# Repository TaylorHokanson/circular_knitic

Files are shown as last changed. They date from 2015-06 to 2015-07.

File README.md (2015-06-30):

Original design (c) 2014 Varvara Guljajeva & Mar Canet. See below for original Readme text.

Design changes/suggestions offered by Assistant Professors Taylor
Hokanson and Dieter Kirkwood, who are currently working on a build at
Columbia College Chicago. For more info on this and related machine
knitting projects, see
http://taylorhokanson.com/category/research/hardware/machine-knitting/

All files marked WIP = work in progress (unfinished) 

===============

Circular Knitic, an open hardware knitting machine. 
Project video: https://www.youtube.com/watch?v=-GFXAGRynNM

When building the machine, it is crucial to have the parts 3D printed precisely. Hence, print the parts in High Quality.
We have printed our machine with Ultimaker2, Makerbot Replicator 2, Makerbot Replicator 2x, and RepRapBcn+. Since reprap is not so preciase, some STL files are names as ...REP, which we have altered for that printer.

For laser cutting we have used 5mm and 6mm plexiglass. Use 6mm one for the gears, file gear-up.ai. For the rest use 5mm plexiglass.

We are doing workshops to build one or more machines in one day, if you are interested hosting a workshop please let us know:
varvarag@gmail.com  or mar.canet@gmail.com See photos from WeMake Milano Makerspace workshop done in February 2015: https://www.flickr.com/photos/mcanet/sets/72157650274803049/

Copyright (c) 2014 Varvara Guljajeva & Mar Canet

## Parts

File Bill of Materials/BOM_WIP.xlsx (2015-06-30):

Budget - Circular Knitic
description | real price | quantity | total | link
needles | €0.45 | 100 | €45.00 | http://www.bsk.co.uk/knitmastersilver-reed-sk120--sr120-xkn8-763-p.asp
stepper motor nema23 | €50.00 | 1 | €24.95 | https://www.pololu.com/product/1476 | DK
Big Easy stepper motor Driver | €20.00 | 1 | €19.95 | https://www.sparkfun.com/products/12859 | DK
Arduino Uno | €21.00 | 1 | €21.00
ventilator 12v 40mm x 40mm | €6.00 | 1 | €8.95 | http://www.jameco.com/webapp/wcs/stores/servlet/ProductDisplay?productId=1928118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 | DK
power supply 12v | €20.00 | 1 | €20.00
cabling | €8.00 | 1 | €8.00
carbon fiber tensor 2mm | €1.00 | 1 | €1.00 | http://www.mwmaterialsworld.com/es/barra-fibra-de-carbono.html | I think this is for the yarn tension unit. not needed
bearings (bore 5mm x 10mm x 4mm) | €0.60 | 14 | €16.00 | http://www.ebay.com/itm/10pcs-Axial-Ball-Thrust-Bearing-F5-10M-5mm-x-10mm-x-4mm-5-x-10-x-4-mm-/290699007785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 | DK
screws and nuts | €10.00 | 1 | €10.00
shaft of motor | €7.00 | 1 | €4.95 | http://www.pololu.com/product/2675 | DK
switch | €4.00 | 1 | €4.00
paper clips | €0.01 | 30 | €0.30
Plexiglas 5mm | €10.00 | 2 | €20.00 | http://proplastik.ee
Plexiglas 6mm | €11.00 | 1 | €11.00 | http://proplastik.ee
filament | €38.00 | 1 | €38.00
makerbeam 150mm | €2.20 | 2 | €4.40 | http://www.amazon.com/MakerBeam-200mm-beam-black-anodised/dp/B00G2DNTLQ?s=industrial | DK
makerbeam 60mm | €0.80 | 1 | €0.80 | included above
makerbeam 40mm | €0.60 | 1 | €0.60 | included above
makerbeam screws | €3.00 | 1 | €3.00 | 3d print these
makerbeam Lshape | €0.90 | 5 | €4.50 | http://www.amazon.com/MakerBeam-90-degree-brackets-pack/dp/B00G2DNV0U | BUY AT HOMEDEPOT? DK
wood structure | €25.00 | 1 | €25.00
claw weight | €6.00 | 4 | €24.00
paraphine | €2.00 | 1 | €2.00
 |  | Total | €334.00
Manufacturing
3d prints outers | €15.00 | 4 | €60.00
3d print inners | €6.00 | 24 | €144.00
3d print yarnholders | €12.00 | 4 | €48.00
3d print bearring holders | €3.00 | 5 | €15.00
3d print connectors | €1.00 | 15 | €15.00
Lasercutting | €90.00 | 0.5 | €45.00
 |  | Total | €327.00

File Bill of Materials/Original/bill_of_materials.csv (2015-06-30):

Budget - Circular Knitic
description | real price | quantity | total | link
needles | €0.45 | 100 | €45.00 | http://www.bsk.co.uk/knitmastersilver-reed-sk120--sr120-xkn8-763-p.asp
stepper motor nema23 | €50.00 | 1 | €50.00
Big Easy stepper motor Driver | €20.00 | 1 | €20.00
Arduino Uno | €21.00 | 1 | €21.00
ventilator 12v 40mm x 40mm | €6.00 | 1 | €6.00
power supply 12v | €20.00 | 1 | €20.00
cabling | €8.00 | 1 | €8.00
carbon fiber tensor 2mm | €1.00 | 1 | €1.00 | http://www.mwmaterialsworld.com/es/barra-fibra-de-carbono.html
bearings (bore 5mm x 10mm x 4mm) | €0.60 | 14 | €8.40
screws and nuts | €10.00 | 1 | €10.00
shaft of motor | €7.00 | 1 | €7.00 | http://www.pololu.com/product/2675
switch | €4.00 | 1 | €4.00
paper clips | €0.01 | 30 | €0.30
Plexiglas 5mm | €10.00 | 2 | €20.00 | http://proplastik.ee
Plexiglas 6mm | €11.00 | 1 | €11.00 | http://proplastik.ee
filament | €38.00 | 1 | €38.00
makerbeam 150mm | €2.20 | 2 | €4.40
makerbeam 60mm | €0.80 | 1 | €0.80
makerbeam 40mm | €0.60 | 1 | €0.60
makerbeam screws | €3.00 | 1 | €3.00
makerbeam Lshape | €0.90 | 5 | €4.50
wood structure | €25.00 | 1 | €25.00
claw weight | €6.00 | 4 | €24.00
paraphine | €2.00 | 1 | €2.00
 |  | Total | €334.00
Manufacturing
3d prints outers | €15.00 | 4 | €60.00
3d print inners | €6.00 | 24 | €144.00
3d print yarnholders | €12.00 | 4 | €48.00
3d print bearring holders | €3.00 | 5.00 | €15.00
3d print connectors | €1.00 | 15 | €15.00
Lasercutting | €90.00 | 0.5 | €45.00
 |  | Total | €327.00

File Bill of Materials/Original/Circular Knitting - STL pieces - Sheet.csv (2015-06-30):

comments | max layer height | Order nr. | Components | # of Pieces
1 and 2 are the same pieces. | 0.06 (recommended) | 1 | BearringBig1212 (repaired).stl | 1
this piece has been made slightly bigger for the reprap printer | 0.15 | 2 | BearringBigREP (repaired).stl | 1
 | 0.06 | 3 | BearringSmall1312 (repaired).stl | 4
 | 0.15 | 4 | Pipe (repaired).stl | 1
 | 0.15 | 5 | YarnHolderPalo.stl | 2
6 and 7 are the same | 0.06 | 6 | Zshape1212 (repaired).stl | 4
made for reprap | 0.15 | 7 | ZshapeRep (repaired).stl | 4
 | 0.1 | 8 | connection0912.stl | 11
 | 0.06 | 9 | inner0112 (repaired).stl | 12
 | 0.1 | 10 | mountain1212 (repaired).stl | 1
 | 0.15 | 11 | outer2511 (repaired).stl | 4
 | 0.1 | 12 | outerNeedleConnector (repaired).stl | 4
 | 0.1 | 13 | yarnHolder0212 (repaired).stl | 4
*print all parts in 'High Quality' (the option that your slicr program has).
Max layer height 0.1mm and infill 15% or 20%.
With layer height 0.06 no filing is required

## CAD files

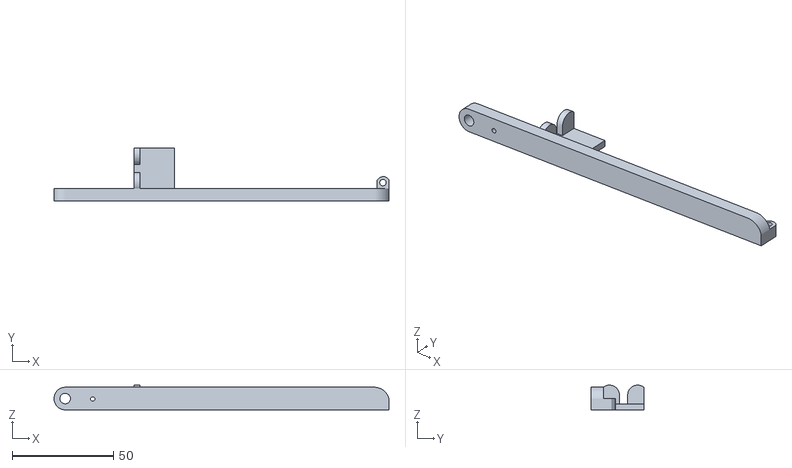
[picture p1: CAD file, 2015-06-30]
Fabrication/3D Printing/Original STLs/yarnTensioner1.stl
165.3 x 26.0 x 12.3

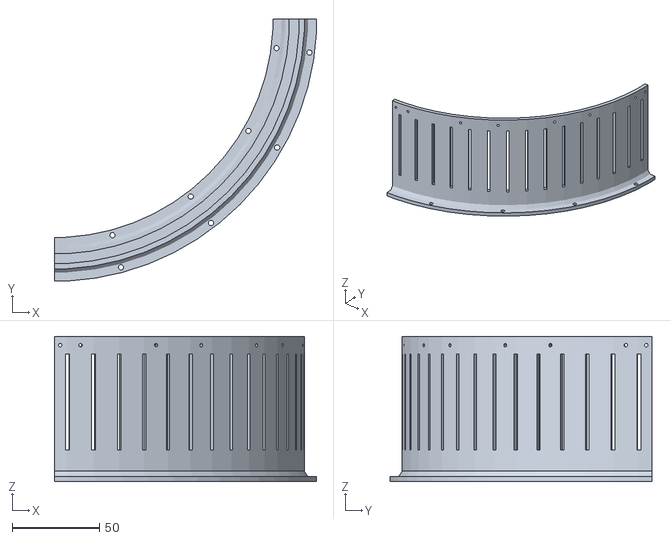
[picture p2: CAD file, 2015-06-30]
Fabrication/3D Printing/Original STLs/outer2511_x_4.stl
149.8 x 149.8 x 83.0

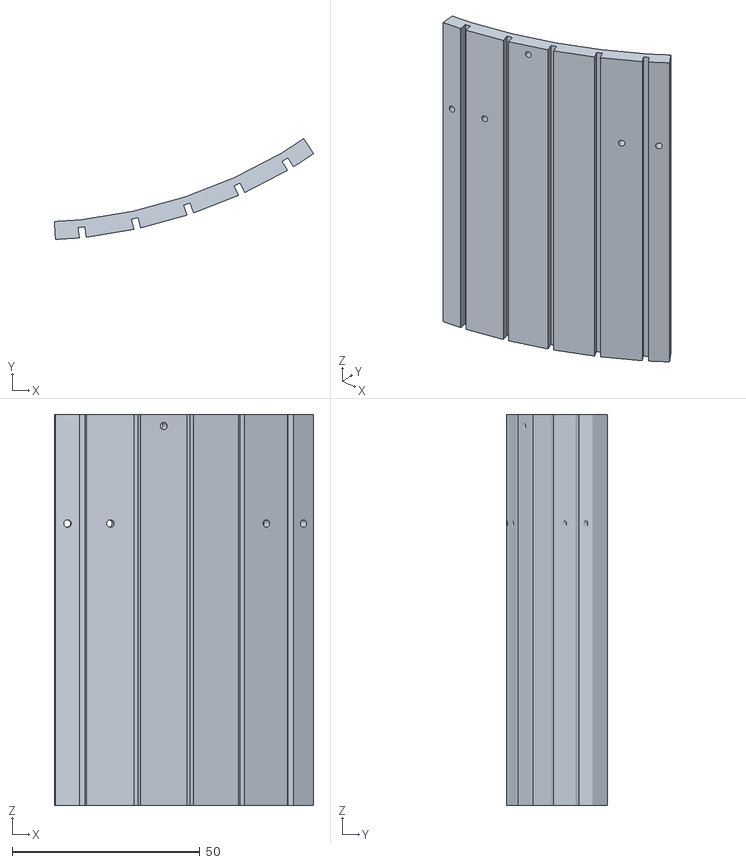
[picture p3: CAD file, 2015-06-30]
Fabrication/3D Printing/Original STLs/inner0112_x_12.stl
69.0 x 26.8 x 104.0

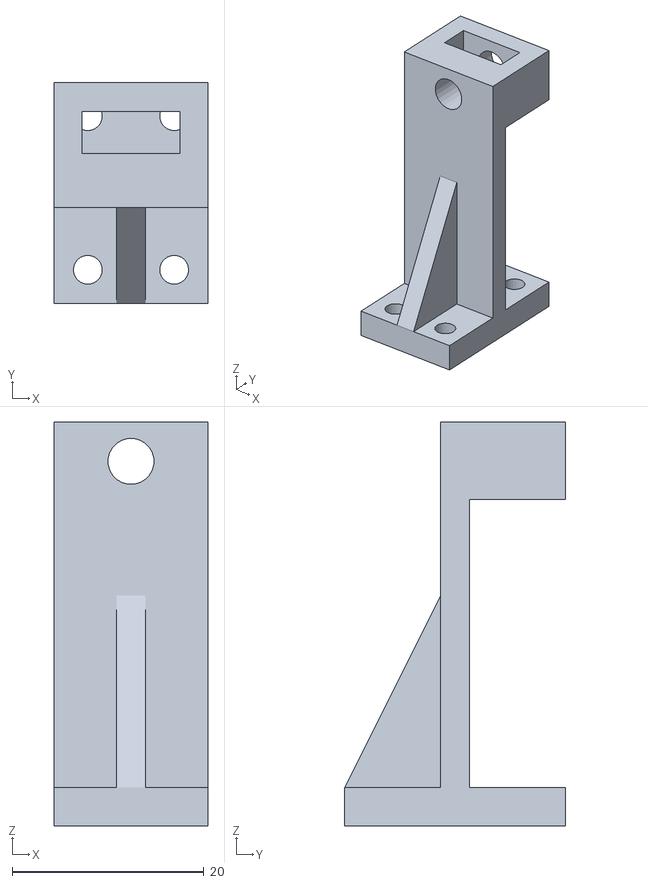
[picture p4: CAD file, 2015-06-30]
Fabrication/3D Printing/Original STLs/Zshape1212_x_4.stl
16.0 x 23.0 x 42.1

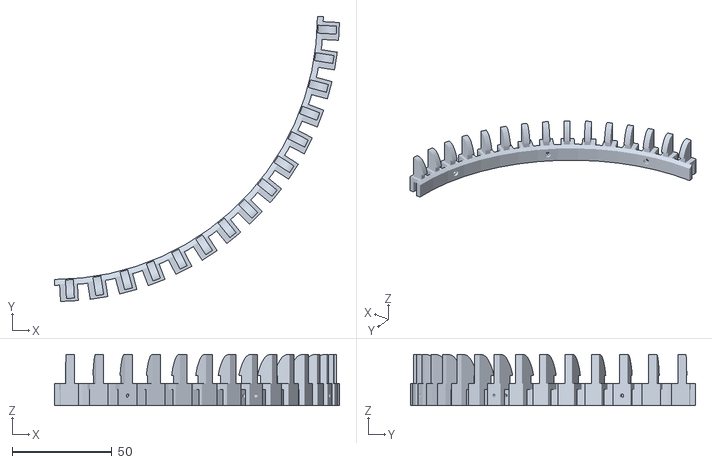
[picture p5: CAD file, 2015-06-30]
Fabrication/3D Printing/Original STLs/yarnHolder0212_x_4.stl
142.9 x 142.9 x 25.6

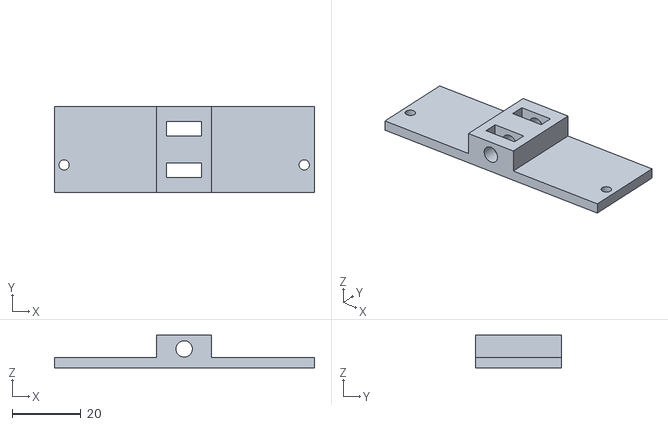
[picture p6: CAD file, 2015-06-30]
Fabrication/3D Printing/Original STLs/BearringBig1212 (repaired).stl
75.8 x 25.0 x 9.50

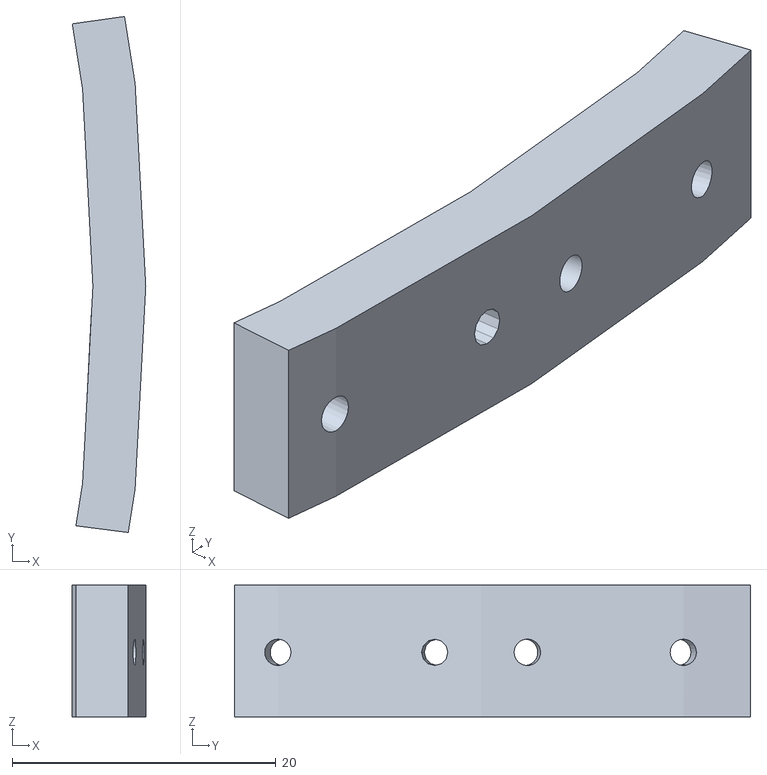
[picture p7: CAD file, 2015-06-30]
Fabrication/3D Printing/Original STLs/outerConnector_x_4.stl
5.57 x 39.1 x 10.0

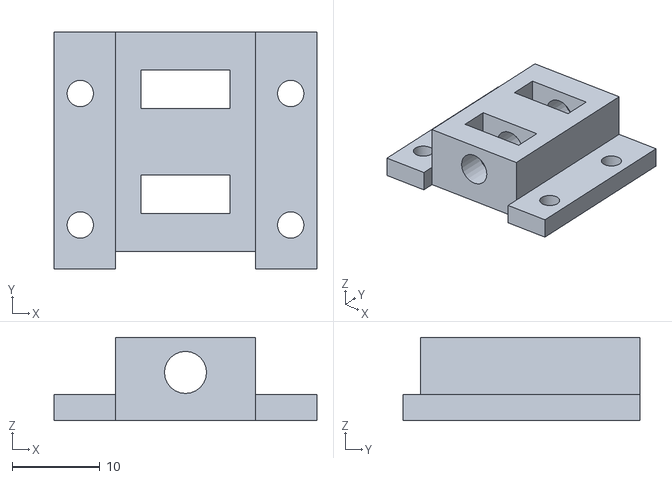
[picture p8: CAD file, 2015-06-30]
Fabrication/3D Printing/Original STLs/BearringSmall1312_x_4.stl
30.0 x 27.0 x 9.50

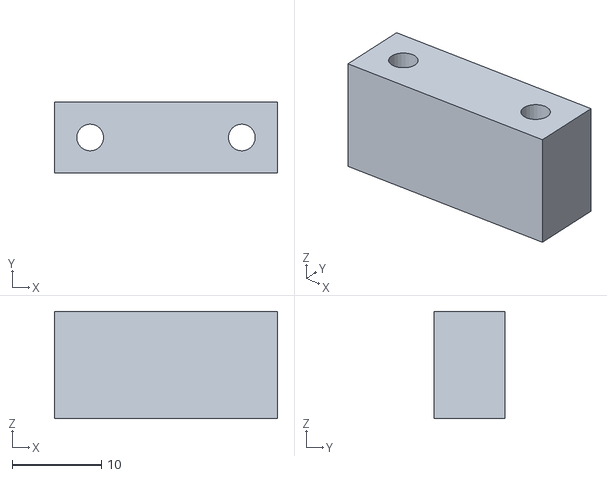
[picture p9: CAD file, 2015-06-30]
Fabrication/3D Printing/Original STLs/connection0912_x_11.stl
25.0 x 8.00 x 12.0

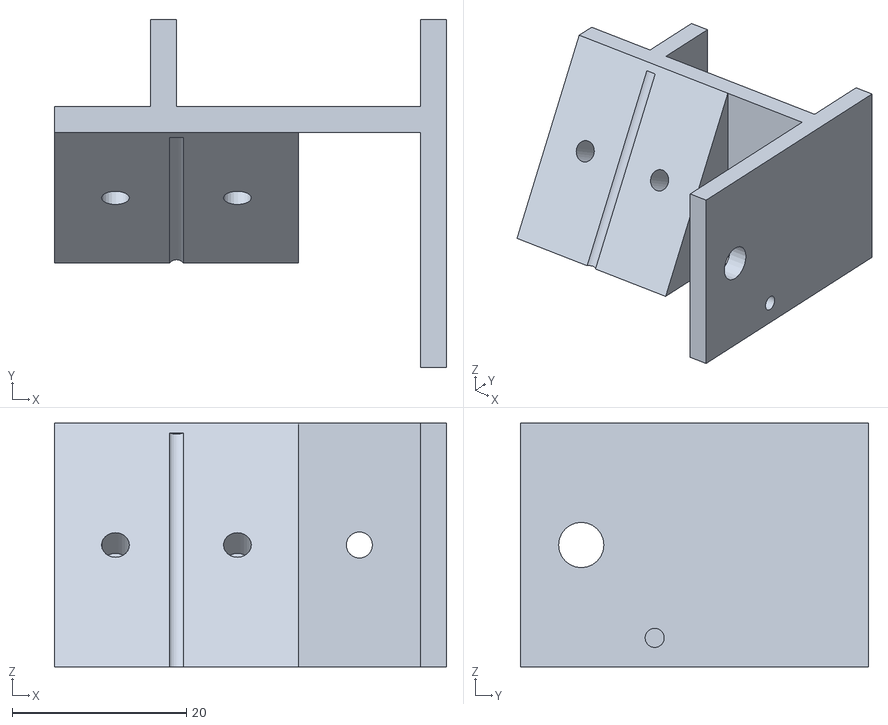
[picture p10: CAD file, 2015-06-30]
Fabrication/3D Printing/Original STLs/yarnfeederSupport.stl
45.0 x 40.0 x 28.0

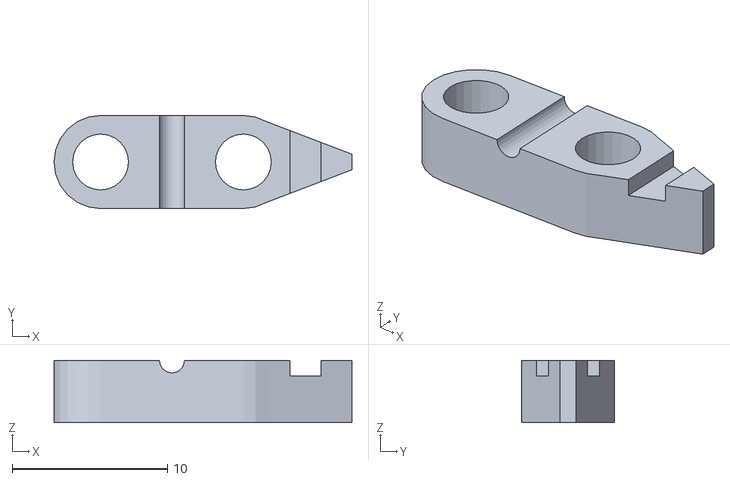
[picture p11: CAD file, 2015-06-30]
Fabrication/3D Printing/Original STLs/YarnHolderPalo_x_2.stl
19.2 x 6.00 x 4.00

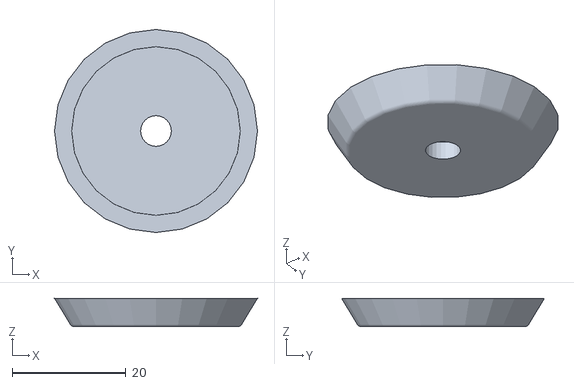
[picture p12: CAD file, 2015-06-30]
Fabrication/3D Printing/Original STLs/spring.stl
35.7 x 35.7 x 5.00

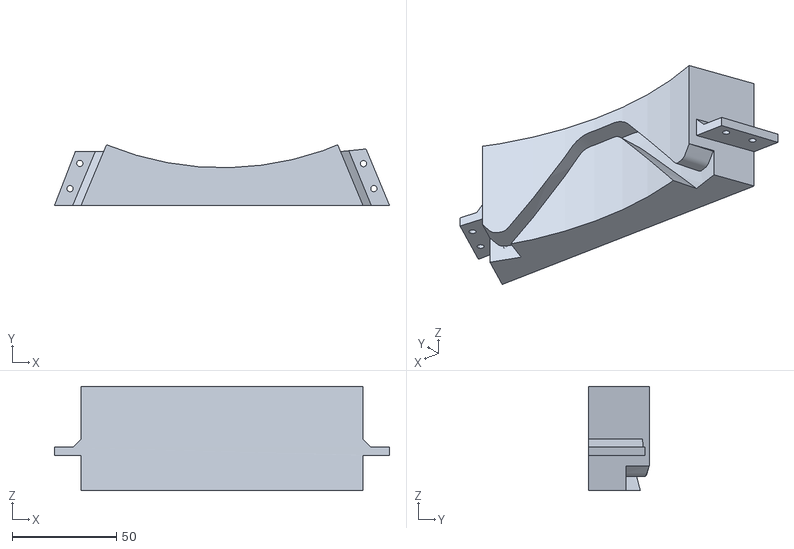
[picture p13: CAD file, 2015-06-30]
Fabrication/3D Printing/Original STLs/mountain1212 (repaired).stl
160.9 x 29.1 x 50.0

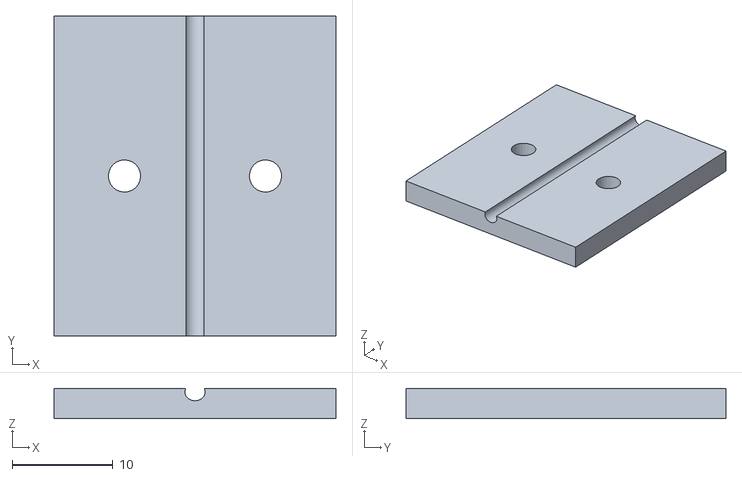
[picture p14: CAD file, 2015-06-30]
Fabrication/3D Printing/Original STLs/YarnTensonerHolder300315.stl
28.0 x 31.8 x 3.00

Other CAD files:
Fabrication/3D Printing/Original STLs/ZshapeRep_x_4.stl
Fabrication/3D Printing/Original STLs/BearringBigREP (repaired).stl
Fabrication/3D Printing/3DM/1.3dm
Fabrication/3D Printing/3DM/2.3dm
Fabrication/3D Printing/3DM/3.3dm
Fabrication/3D Printing/3DM/4.3dm
Fabrication/3D Printing/3DM/5_WIP.3dm
Fabrication/3D Printing/3DM/6.3dm
Fabrication/3D Printing/3DM/Mountain.3dm
_CircularKnitic.skp

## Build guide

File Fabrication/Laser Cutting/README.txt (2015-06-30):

All cuts made in 5.5mm/.25" acrylic
Cut order is Red, Green, Blue
You only need one gear, but we cut extras because they kept breaking teeth before everything was lubed and running smoothly

Changes:
All cuts distributed in the layers of one document
Color coded cut order
Deleted unused gears (for our BOM)
Deleted electronics housing (will post a different solution)
Reoriented stepper motor mount, control panel

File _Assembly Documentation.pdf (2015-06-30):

open source knitting machine
http://var-mar.info | http://www.knitic.com

Varvara Guljajeva & Mar Canet

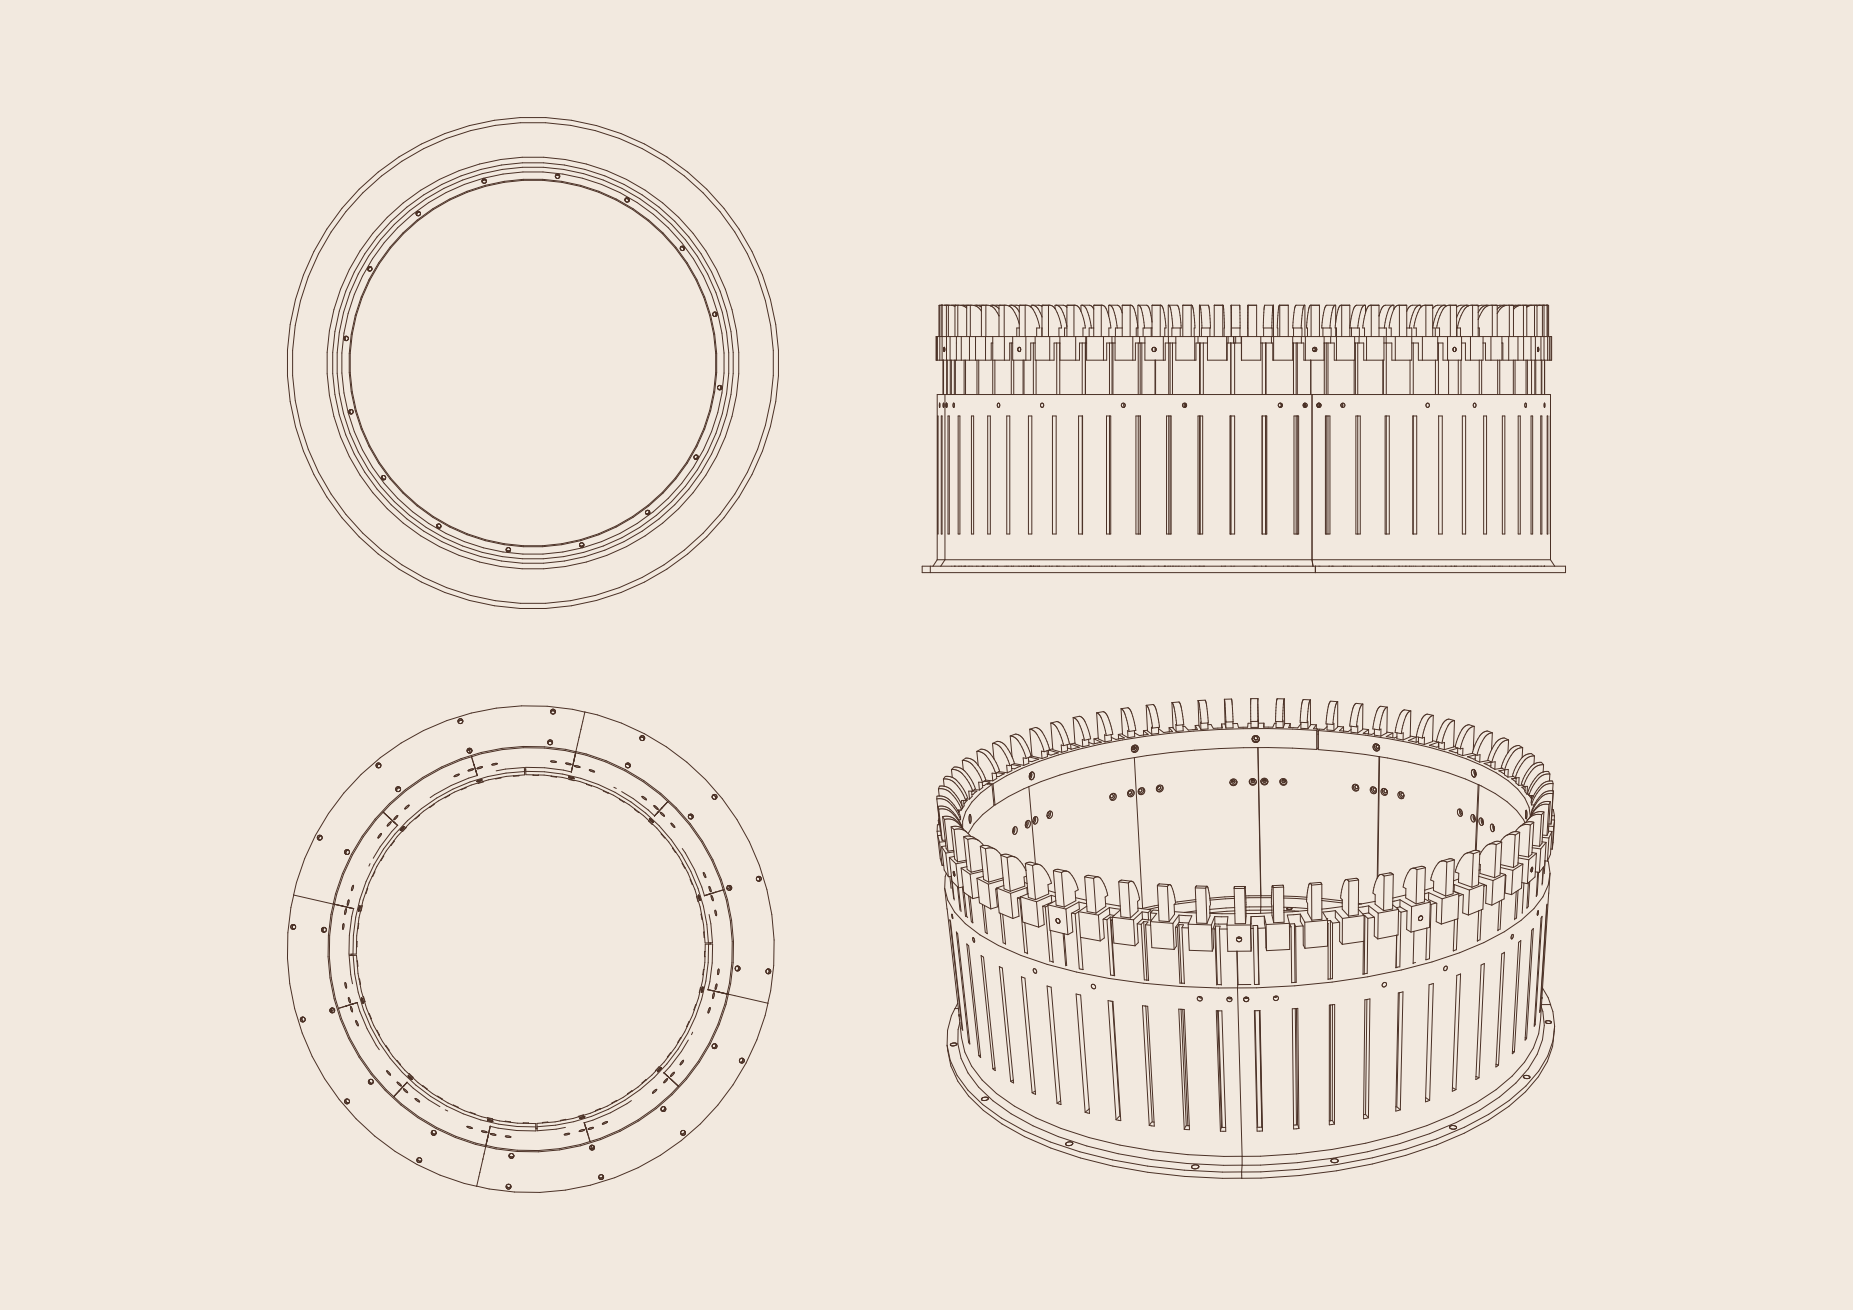
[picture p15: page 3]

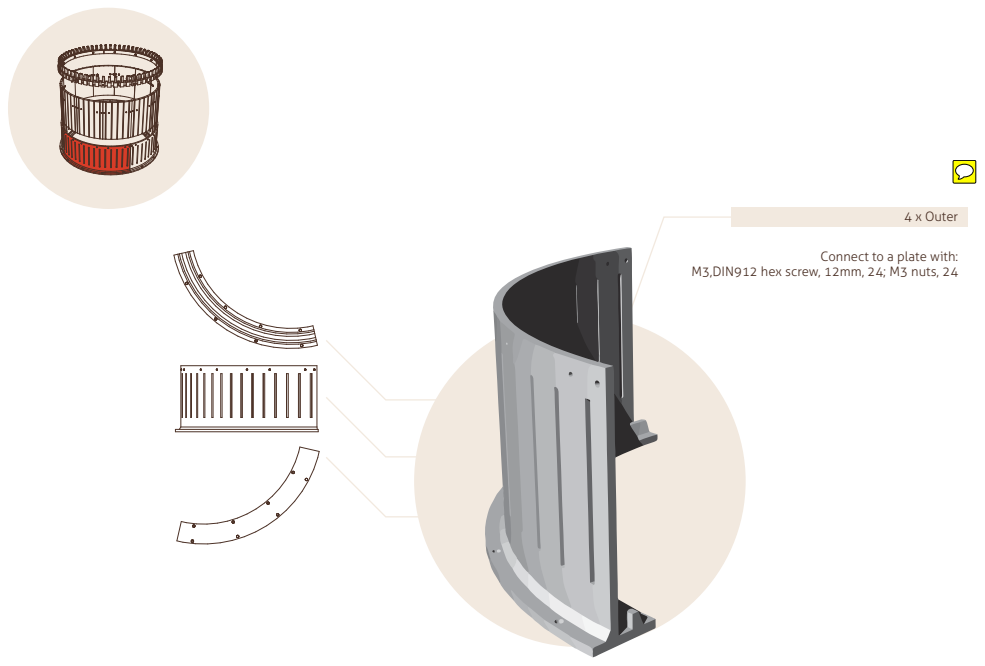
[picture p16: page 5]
4 x Outer

Connect to a plate with:

M3,DIN912 hex screw, 12mm, 24; M3 nuts, 24

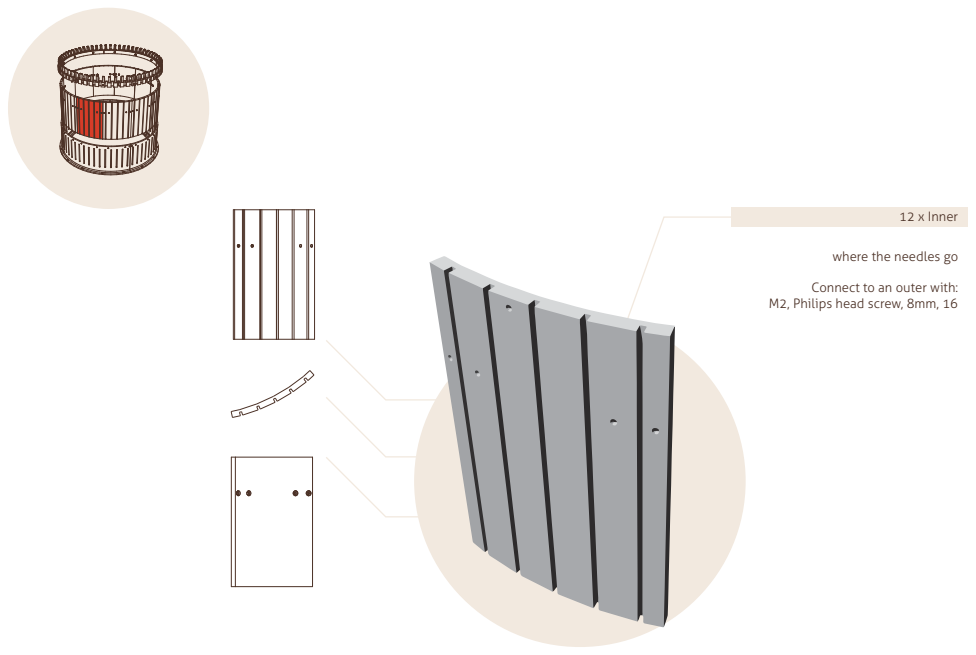
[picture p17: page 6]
12 x Inner

where the needles go

Connect to an outer with:
M2, Philips head screw, 8mm, 16

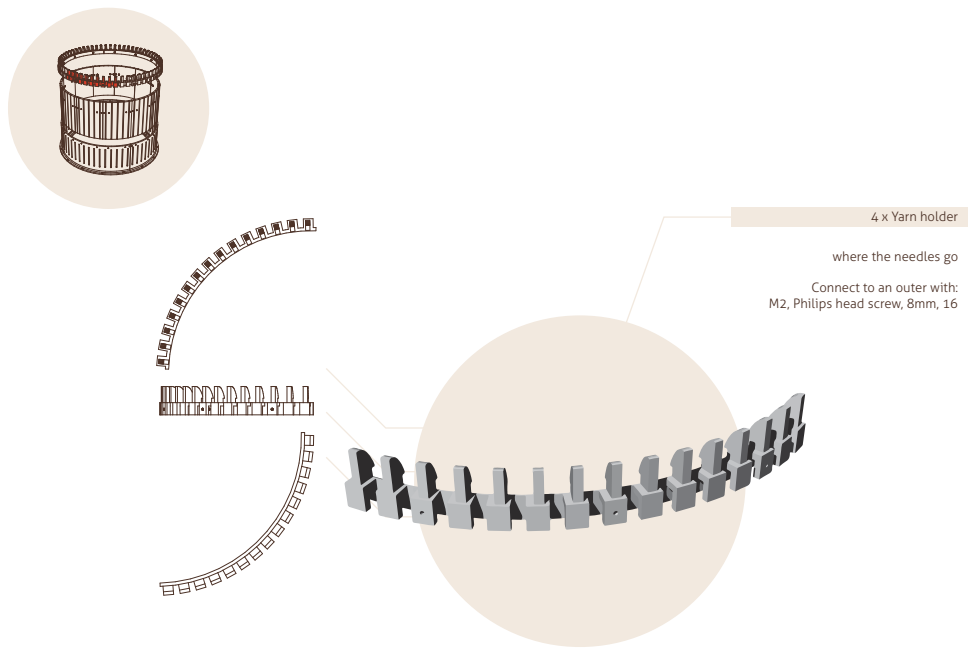
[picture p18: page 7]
4 x Yarn holder

where the needles go

Connect to an outer with:
M2, Philips head screw, 8mm, 16

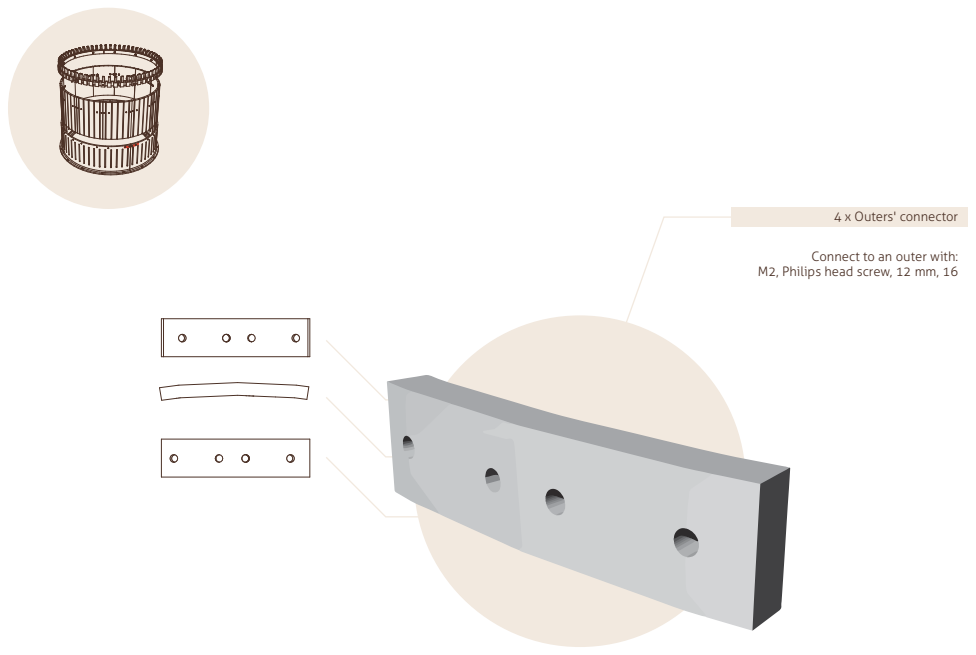
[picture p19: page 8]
4 x Outers' connector

Connect to an outer with:

M2, Philips head screw, 12 mm, 16

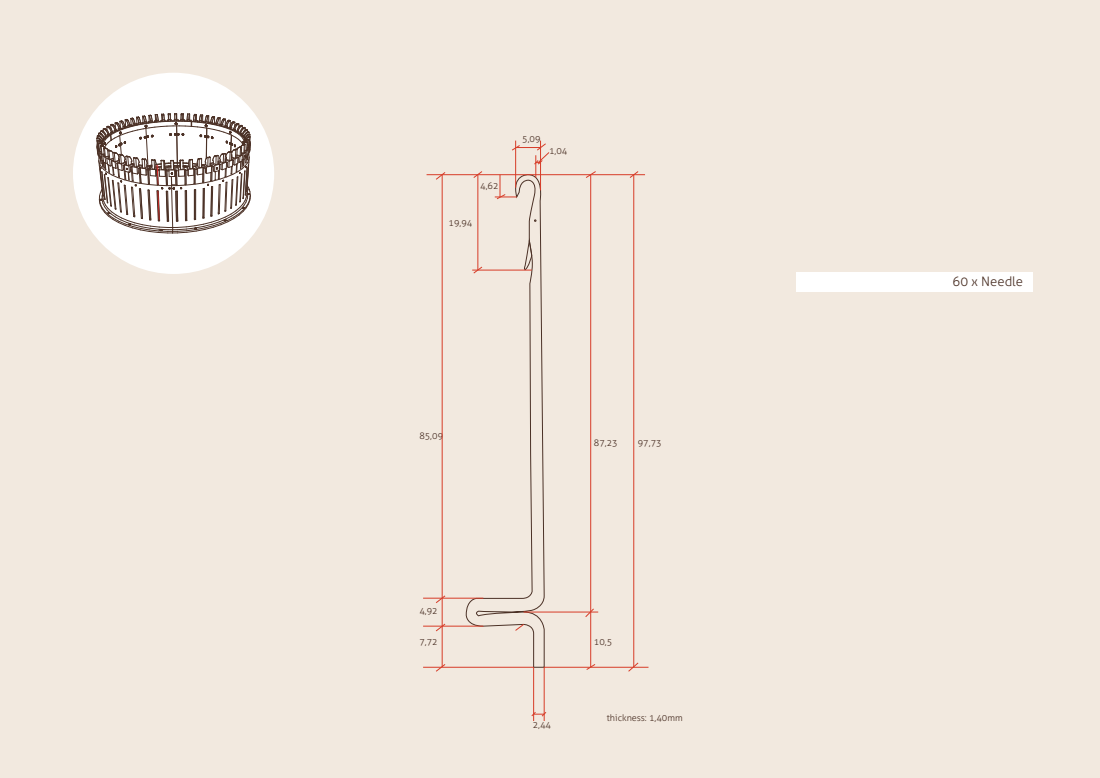
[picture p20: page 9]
60 x Needle; thickness: 1,40mm

Bottom surface (big gear) + motor gears

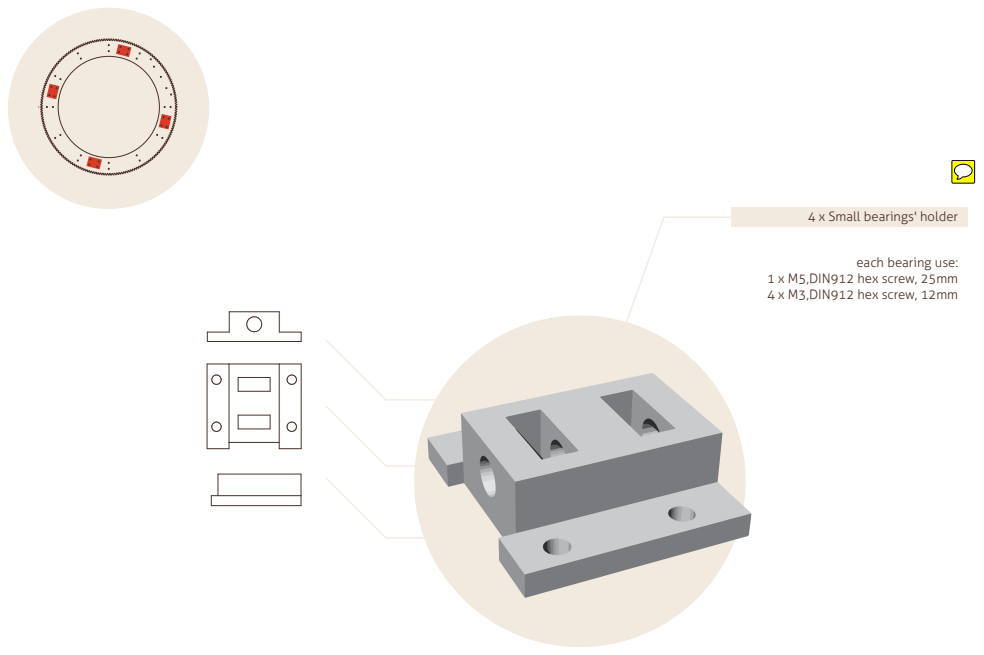
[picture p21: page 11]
1 x M5,DIN912 hex screw, 25mm 4 x M3,DIN912 hex screw, 12mm

4 x Small bearings' holder

each bearing use:

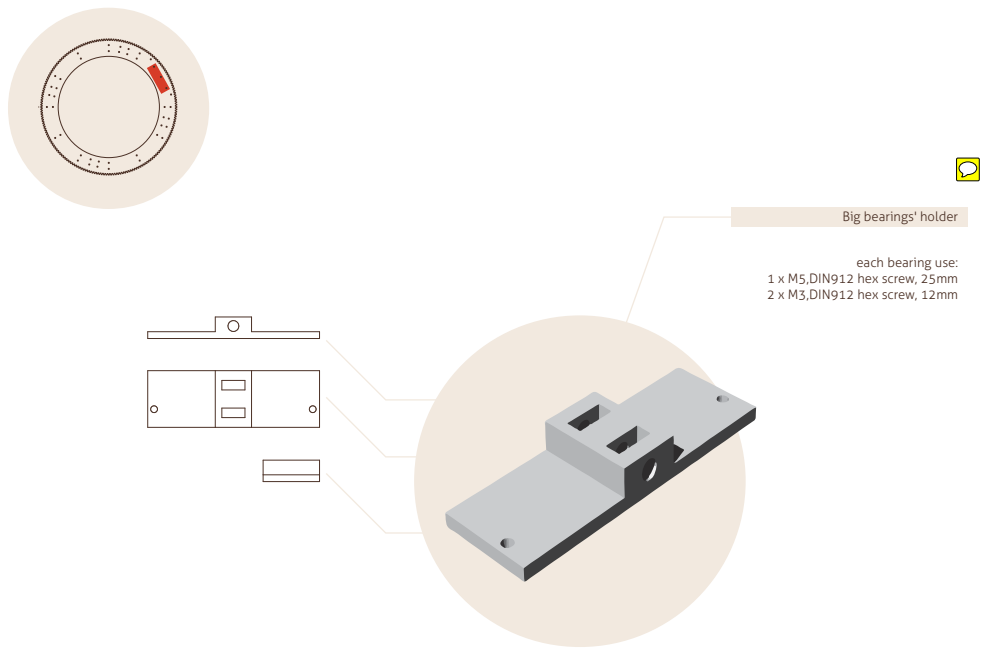
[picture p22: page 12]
1 x M5,DIN912 hex screw, 25mm 2 x M3,DIN912 hex screw, 12mm

Big bearings' holder

each bearing use:

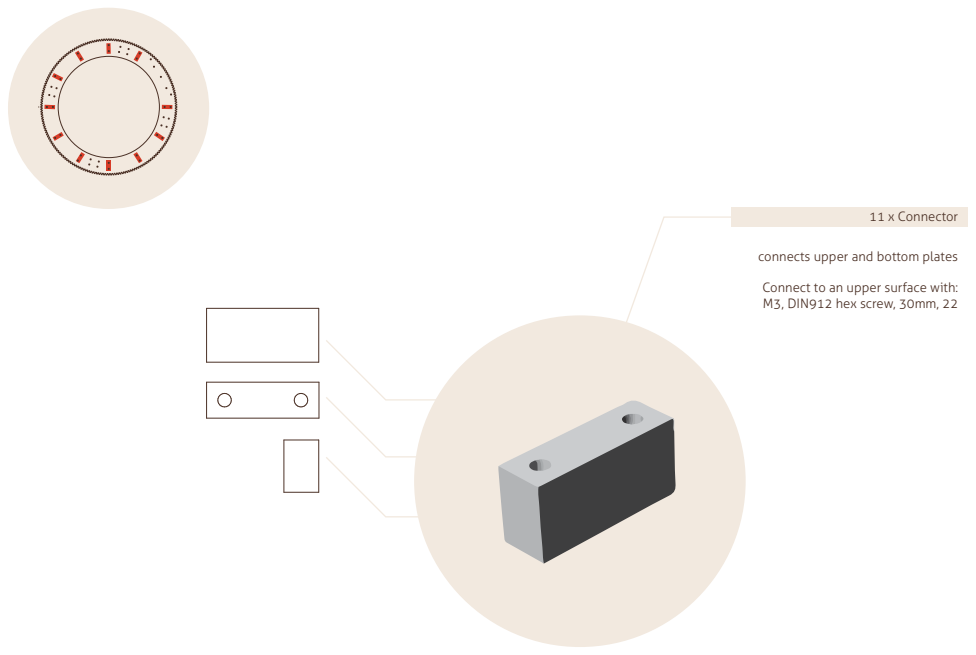
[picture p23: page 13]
11 x Connector

connects upper and bottom plates

Connect to an upper surface with:
M3, DIN912 hex screw, 30mm, 22

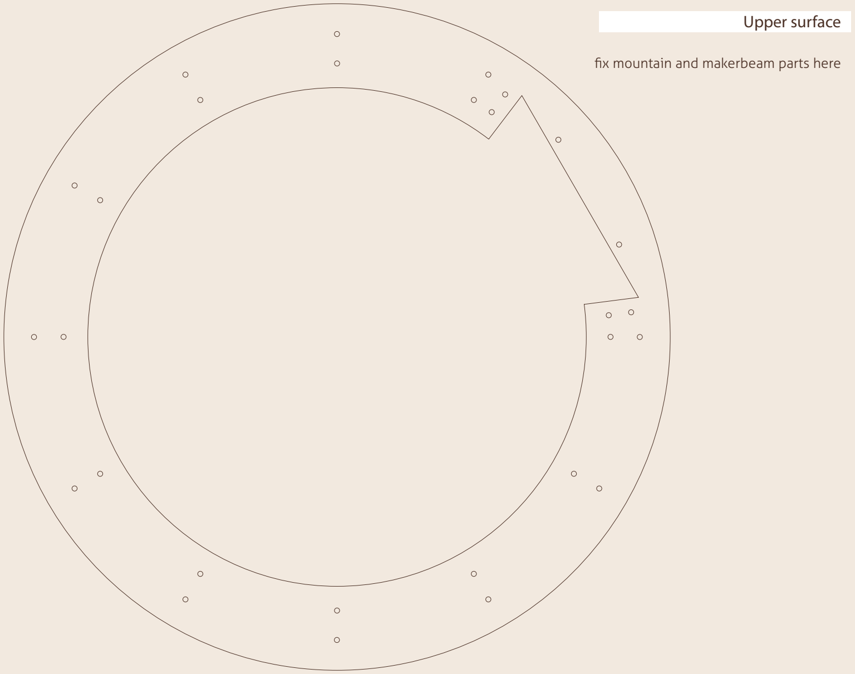
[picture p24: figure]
fix mountain and makerbeam parts here; Upper surface
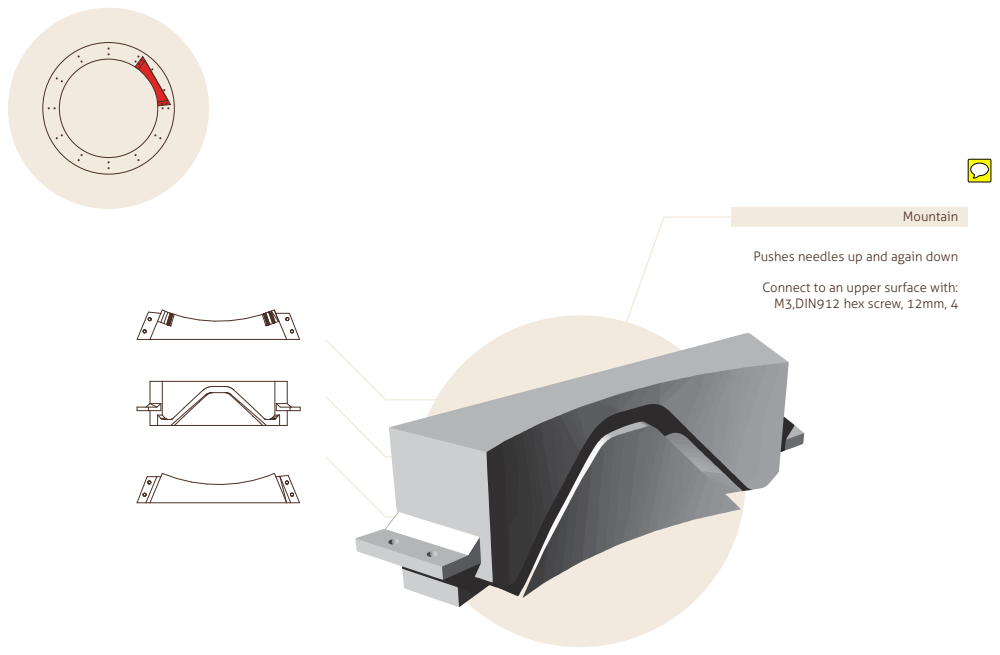
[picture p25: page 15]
Mountain

Pushes needles up and again down

Connect to an upper surface with:
M3,DIN912 hex screw, 12mm, 4

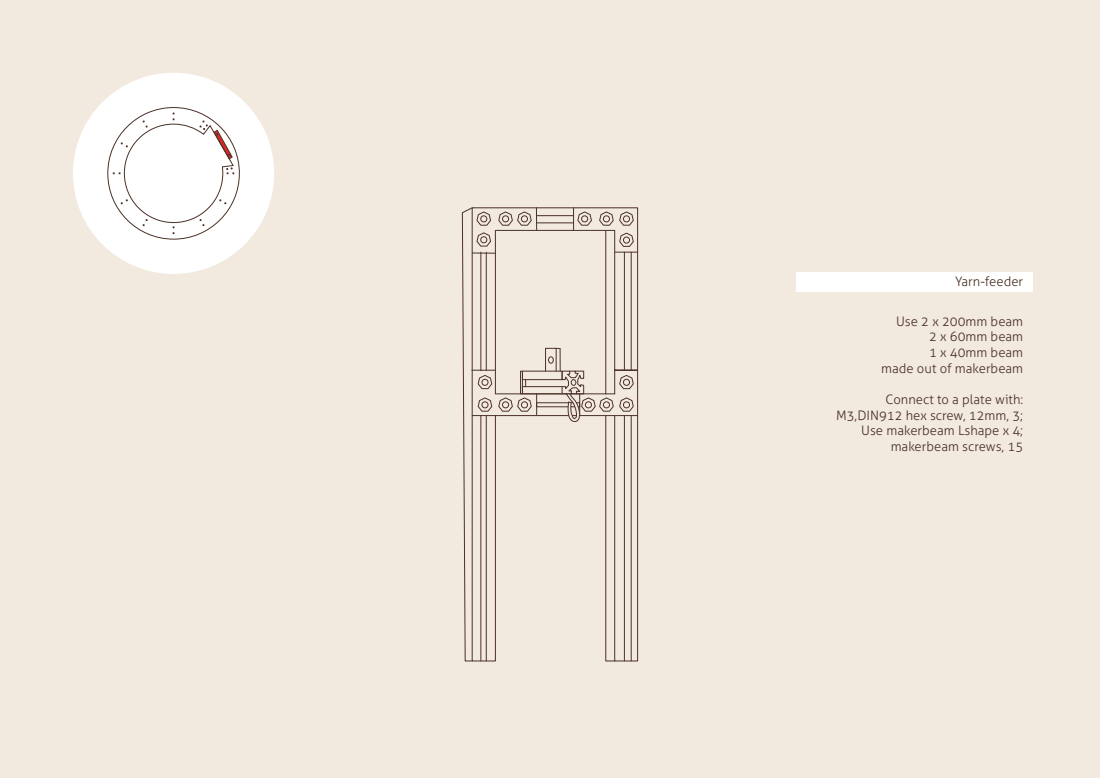
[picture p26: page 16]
Use 2 x 200mm beam 2 x 60mm beam 1 x 40mm beam; Yarn-feeder

made out of makerbeam

Connect to a plate with:

M3,DIN912 hex screw, 12mm, 3;
Use makerbeam Lshape x 4;
makerbeam screws, 15

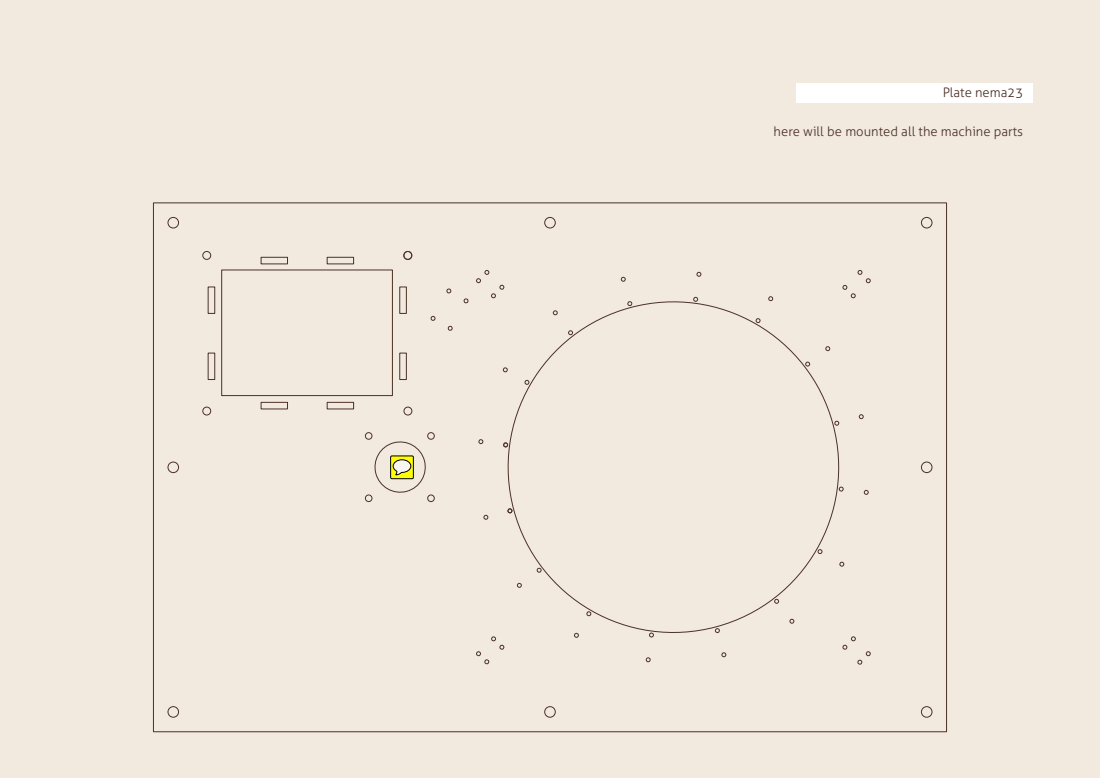
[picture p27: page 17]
Plate nema23

here will be mounted all the machine parts

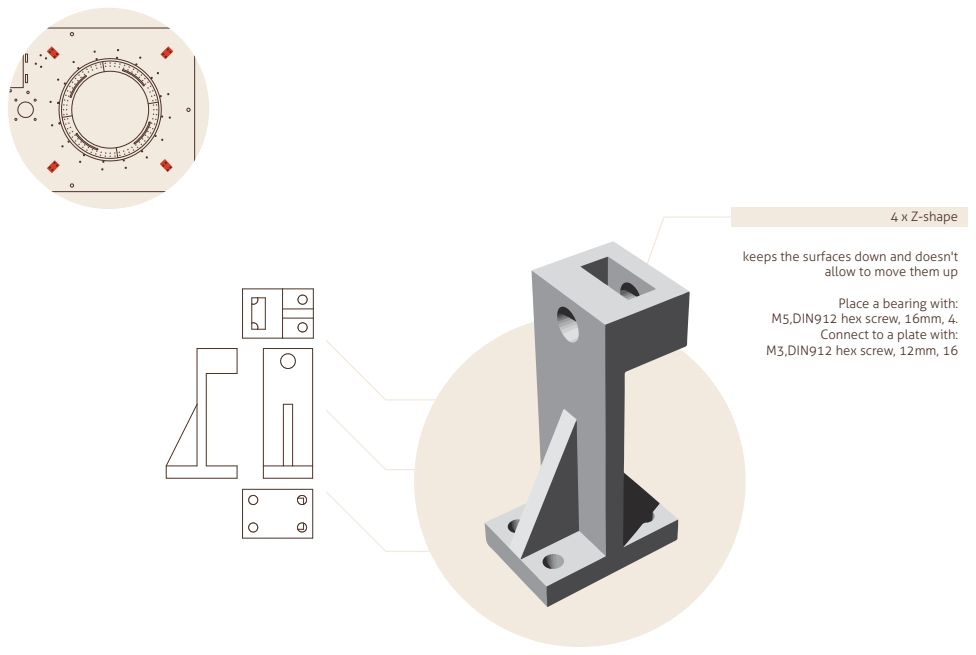
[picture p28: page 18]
M5,DIN912 hex screw, 16mm, 4.; M3,DIN912 hex screw, 12mm, 16; 4 x Z-shape

keeps the surfaces down and doesn't

allow to move them up

Place a bearing with:

Connect to a plate with:

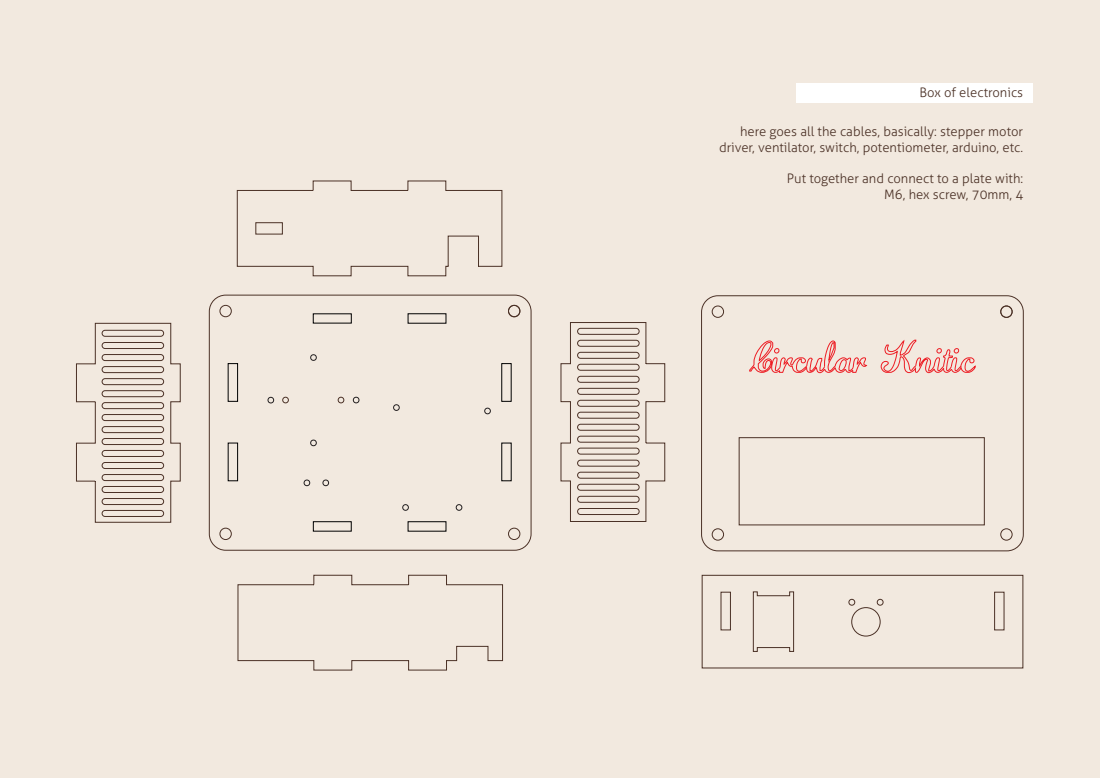
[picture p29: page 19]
M6, hex screw, 70mm, 4

Box of electronics

here goes all the cables, basically: stepper motor
driver, ventilator, switch, potentiometer, arduino, etc.

Put together and connect to a plate with:

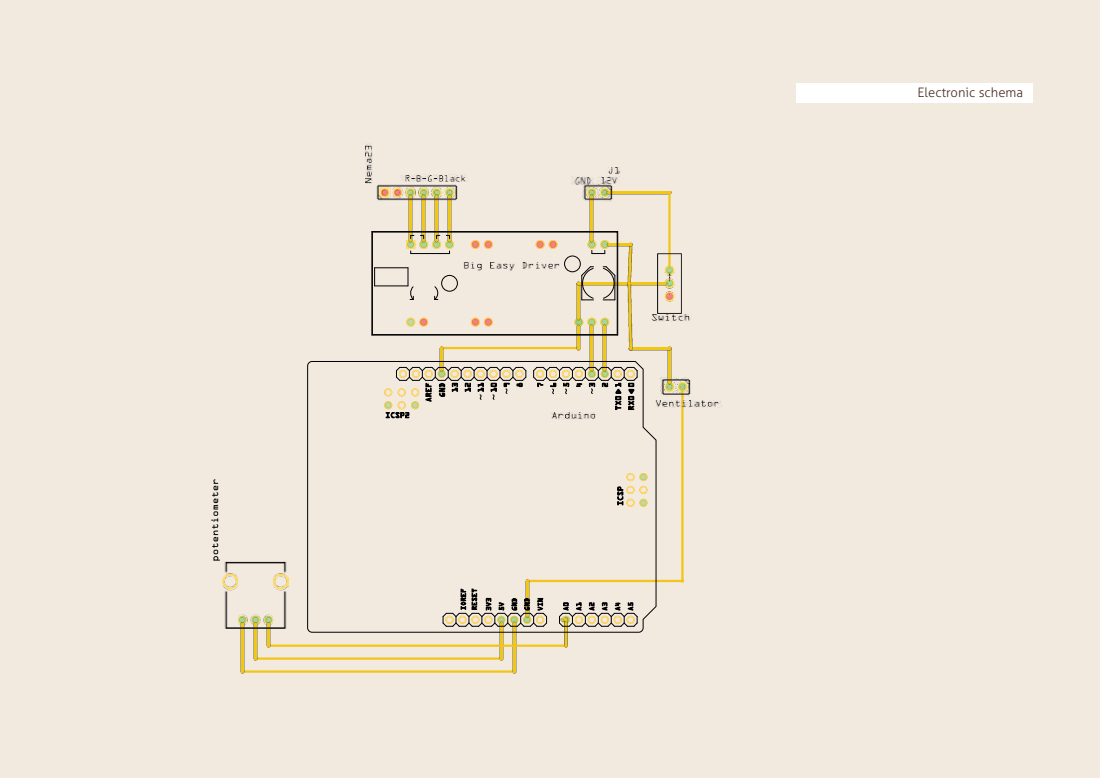
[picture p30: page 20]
Electronic schema

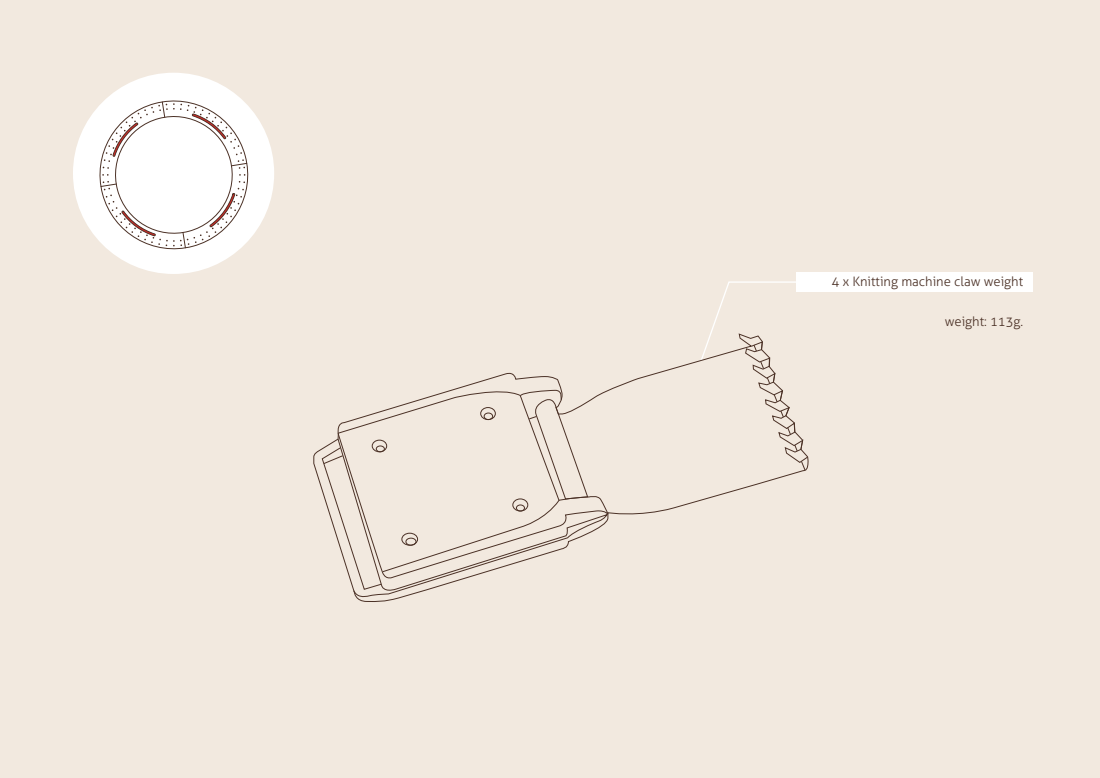
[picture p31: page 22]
weight: 113g.

4 x Knitting machine claw weight

this item fixes a stick, which brings yarn

to the machine, into the table

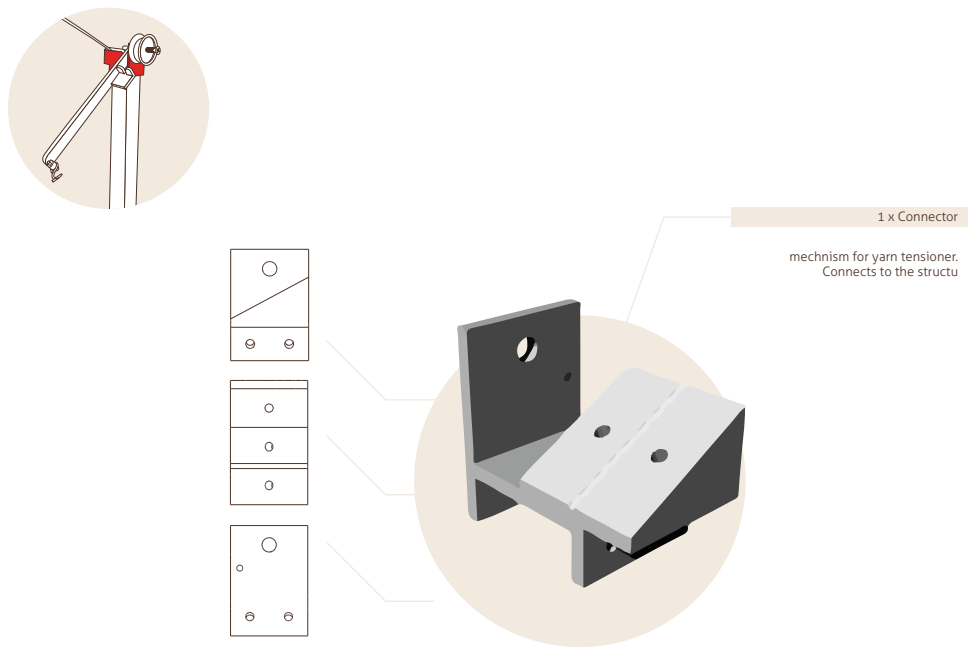
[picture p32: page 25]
1 x Connector

mechnism for yarn tensioner.
Connects to the structu

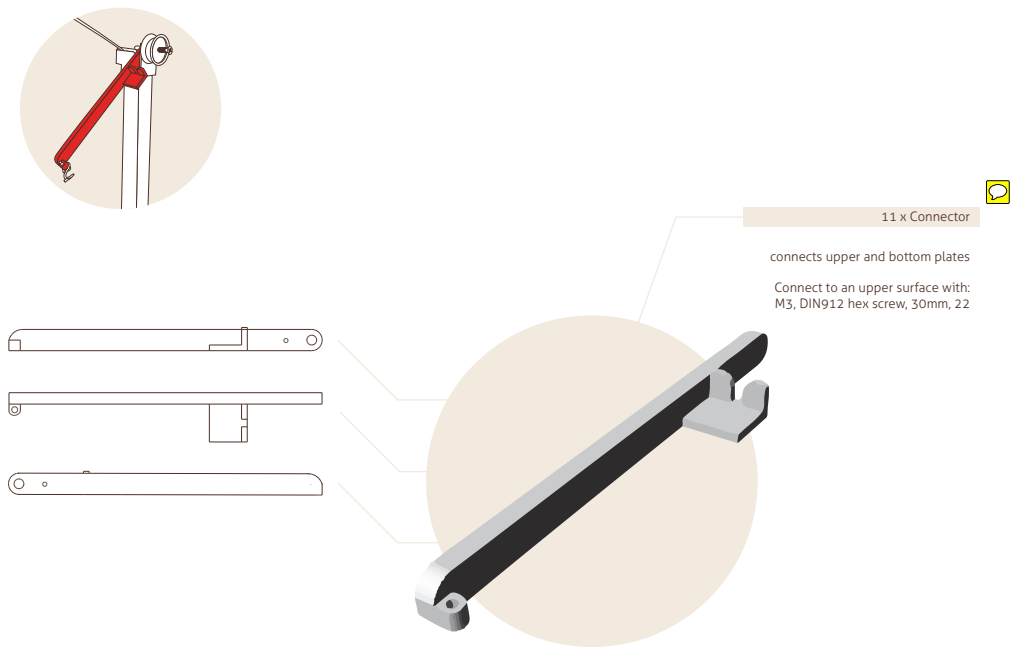
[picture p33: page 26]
11 x Connector

connects upper and bottom plates

Connect to an upper surface with:
M3, DIN912 hex screw, 30mm, 22

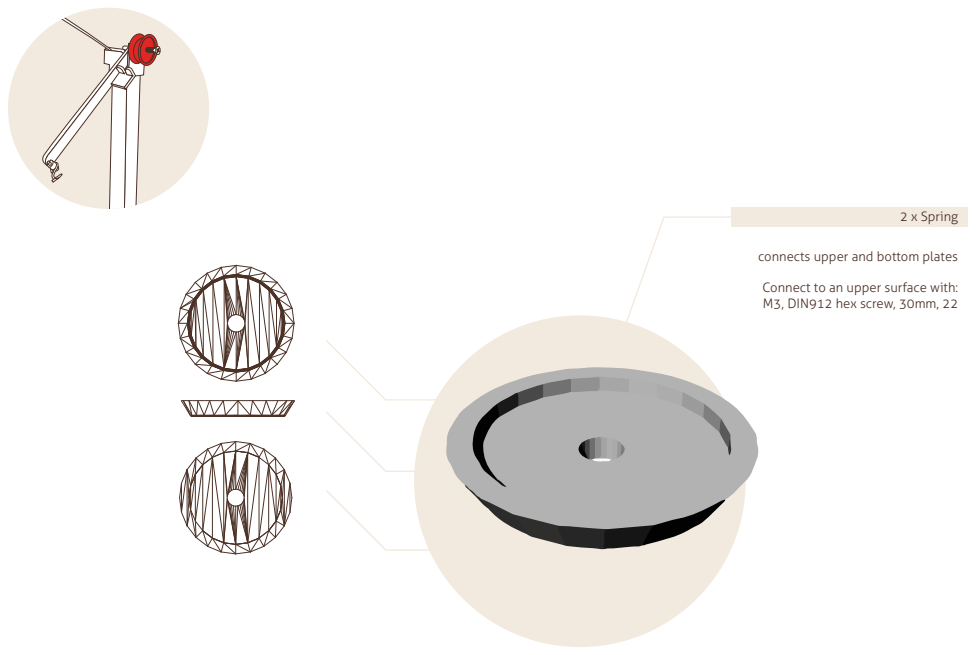
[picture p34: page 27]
2 x Spring

connects upper and bottom plates

Connect to an upper surface with:
M3, DIN912 hex screw, 30mm, 22

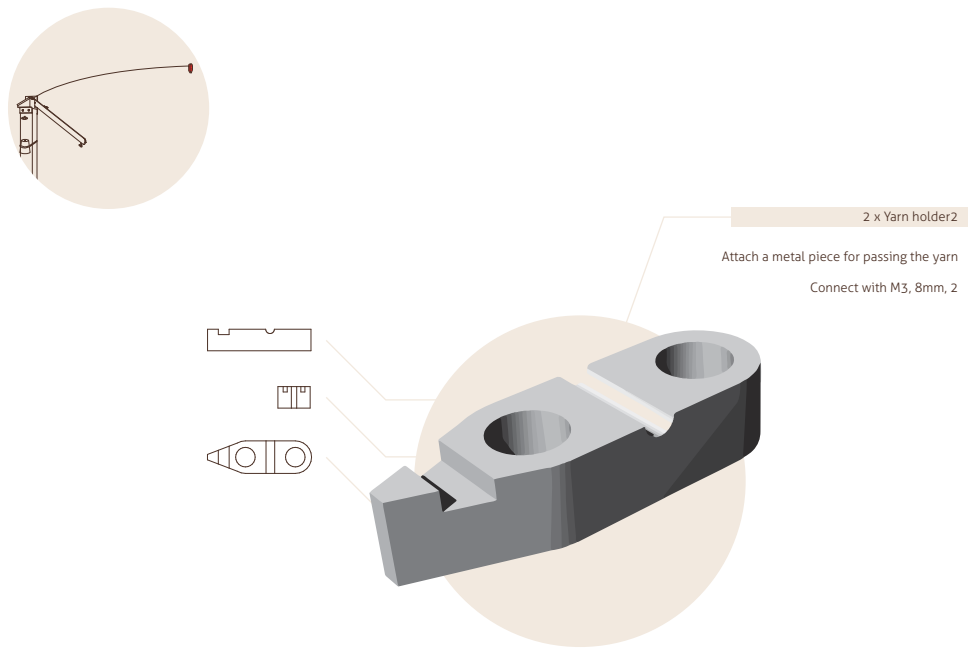
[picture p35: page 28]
Connect with M3, 8mm, 2; 2 x Yarn holder2

Attach a metal piece for passing the yarn

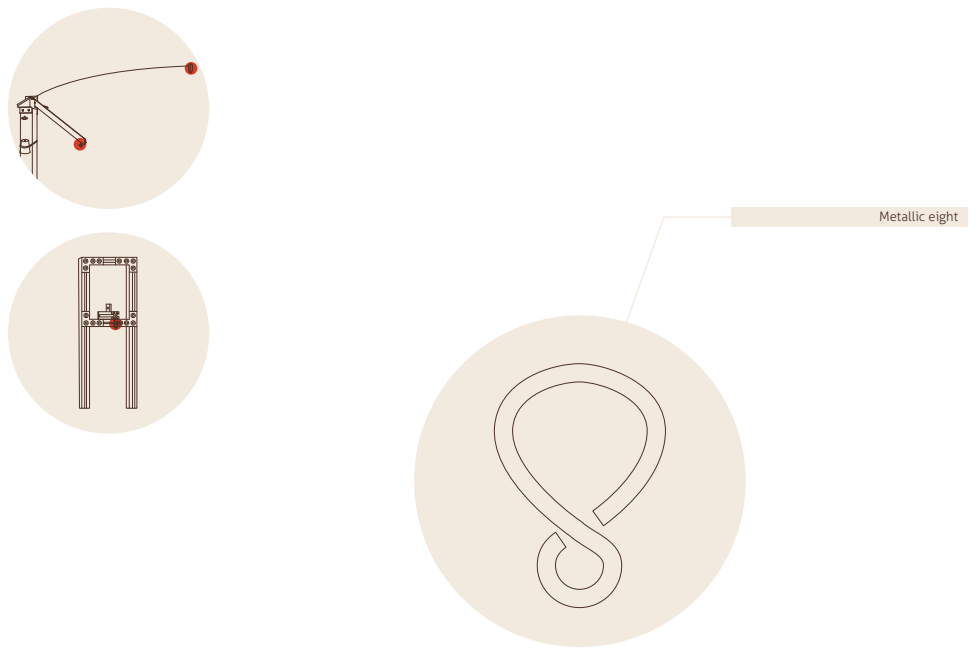
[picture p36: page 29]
Metallic eight

thickness: plate and surfaces

Bottom surface (big gear)

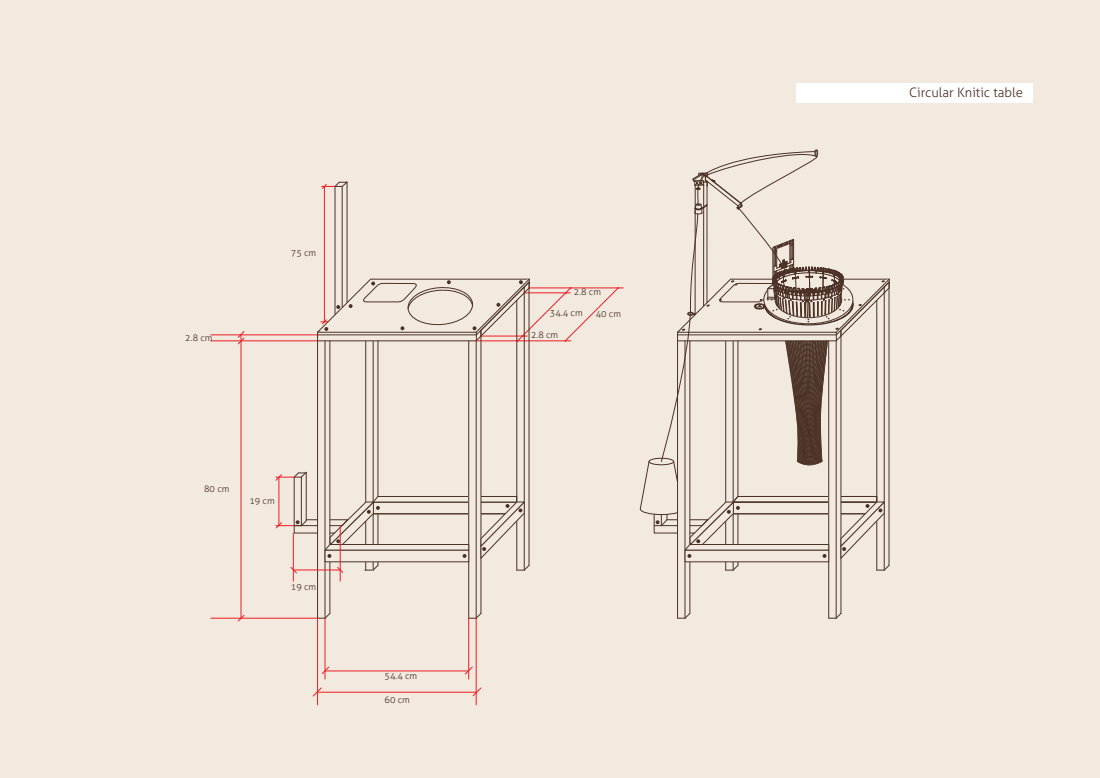
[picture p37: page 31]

Circular Knitic table

### Wood parts to create the machine frame

Other parts

Screws circular Knitic

Others

Size

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
Type

Philips head screw
Philips head screw
steel nut

Screw button head socket
DIN912 hex screw

DIN912 hex screw
DIN912 hex screw
steel nut

DIN912 hex screw
DIN912 hex screw
steel nylon lock nut
Philips head

hex screw
steel nut
wing steel nut

hospa screws

metallic angle | 30x30 x 15 x 2cm | mount wood frame

Long

8mm
12 mm

6mm
12mm

16mm
30mm

16mm
25mm

50mm

70mm

20mm

Quantity

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
attach inners with outer
attach inners with outer connections, yarn holders

makerbeam
attach outers to plexi, and z-shape, small and big bearings’ holders, mountain, construction from makerbeam
attach gear on the stepper motor
attach gear wheel with spacers

attach stepper motor
attach bearing

mount the electronic box
mount the electronic box
mount the electronic box

mount wood frame

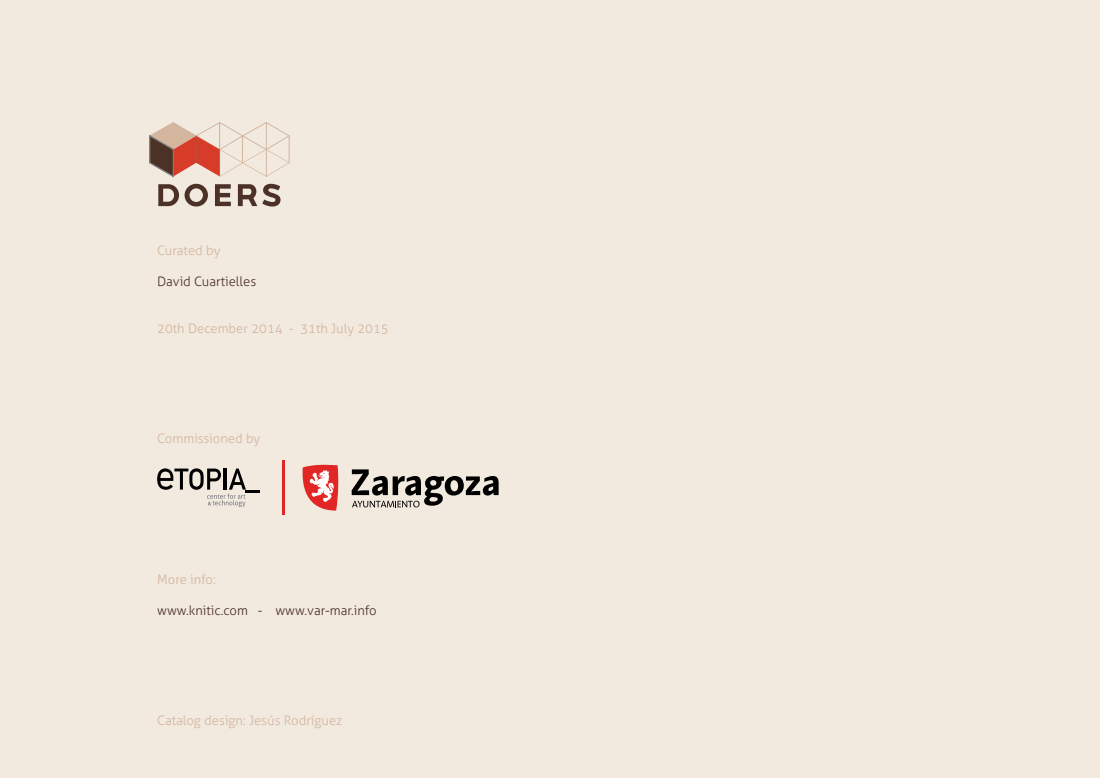
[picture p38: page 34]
Curated by; David Cuartielles; 20th December 2014 - 31th July 2015; Commissioned by; More info:

www.knitic.com - www.var-mar.info

Catalog design: Jesús Rodríguez

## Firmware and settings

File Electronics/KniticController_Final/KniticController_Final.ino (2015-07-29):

// Circular Knitic Controller
// Taylor Hokanson and Dieter Kirkwood
// based on the work of Varvara Guljajeva & Mar Canet

// Button (not implemented): GND > Momentary > Pin 12
// Potentiometer: left pin GND, center pin A0, right pin 5VDC
// Encoder: left pin 3, center pin 2, right pin GND

// Encoder
#include <Encoder.h>
Encoder eKnob(2, 3);
long oldKnobPos  = -999;
long newKnobPos = 0;

// Pot
int newPotVal;
int oldPotVal;
int motorSpeed = 0;
int motorJam = 0;

// Button
const int buttonPin = 12;    // the number of the pushbutton pin
const int ledPin = 13;      // the number of the LED pin
int ledState = LOW;          // start button state LOW (motor forward)
int buttonState;             // the current reading from the input pin
int lastButtonState = LOW;   // the previous reading from the input pin
long lastDebounceTime = 0;  // the last time the output pin was toggled
long debounceDelay = 50;    // the debounce time; increase if the output flickers

//Declare pin functions on Arduino
#define stp 7
#define dir 6
#define MS1 10
#define MS2 9
#define MS3 8
#define EN  11

void setup() {

  // Button
  pinMode(buttonPin, INPUT_PULLUP);
  pinMode(ledPin, OUTPUT);
  digitalWrite(ledPin, ledState);
  
  pinMode(stp, OUTPUT);
  pinMode(dir, OUTPUT);
  pinMode(MS1, OUTPUT);
  pinMode(MS2, OUTPUT);
  pinMode(MS3, OUTPUT);
  pinMode(EN, OUTPUT);
  resetBEDPins();           // Set step, direction, microstep and enable pins to default states

  // Pot
  ADCSRA = 0;
  ADCSRB = 0;
  ADMUX |= (1 << REFS0);                    //set reference voltage
  ADMUX |= (1 << ADLAR);                    //left align the ADC value- so we can read highest 8 bits from ADCH register only
  ADCSRA |= (1 << ADPS2) | (1 << ADPS0);    //set ADC clock with 32 prescaler- 16mHz/32=500kHz
  ADCSRA |= (1 << ADATE);                   //enabble auto trigger
  ADCSRA |= (1 << ADIE);                    //enable interrupts when measurement complete
  ADCSRA |= (1 << ADEN);                    //enable ADC
  ADCSRA |= (1 << ADSC);                    //start ADC measurements
  sei();                                    //enable interrupts

  Serial.begin(9600);
}

// Pot
ISR(ADC_vect) {             //when new ADC value ready
  newPotVal = ADCH;         //update the variable newPotVal with new value from A0 (between 0 and 255)
}

//Main loop
void loop() { 
  checkButton();
  checkPot();
  takeStep();
  checkEncoder();
}

//Reset Big Easy Driver pins to default states
void resetBEDPins()
{
  digitalWrite(stp, LOW);
  digitalWrite(dir, HIGH);  // HIGH = Forward/CCW
  digitalWrite(MS1, LOW);
  digitalWrite(MS2, LOW);
  digitalWrite(MS3, LOW);
  digitalWrite(EN, LOW);    // LOW = Enable Motor Control
}

void checkEncoder(){
  newKnobPos = eKnob.read();
  if (newKnobPos != oldKnobPos) {
    digitalWrite(EN, LOW);    // enable Motor Control
    Serial.print("Encoder = ");
    Serial.print(newKnobPos);
    Serial.println();
    oldKnobPos = newKnobPos;
    motorJam--;
  }else{
    Serial.println("Motor Stopped!\n");
  }
}

void checkPot(){
  if(newPotVal > oldPotVal + 3 || newPotVal < oldPotVal - 3){
    motorSpeed = map(newPotVal, 0, 254, 0, 10); 
    Serial.println("Pot value: " + String(motorSpeed) + "\n");  
    oldPotVal = newPotVal;
  }
}

void checkButton(){
int reading = digitalRead(buttonPin);
  if (reading != lastButtonState) {
    lastDebounceTime = millis();
  }

  if ((millis() - lastDebounceTime) > debounceDelay) {
    if (reading != buttonState) {
      buttonState = reading;
      if (buttonState == HIGH) {
        ledState = !ledState;
      }
    }
  }
  digitalWrite(ledPin, ledState);
  digitalWrite(dir, ledState);
  lastButtonState = reading;
}

void takeStep(){  
  int stepDelay = motorSpeed;
  if (motorJam < 5){
    for(int j= 0; j<5; j++){    //Loop the forward stepping enough times for motion to be visible
      digitalWrite(stp,HIGH);   //Trigger one step forward
      delay(stepDelay);
      digitalWrite(stp,LOW);    //Pull step pin low so it can be triggered again
      delay(stepDelay);
    }
  }
  motorJam++;
  Serial.println("MotorJAm: " + String(motorJam) + "\n");  
}

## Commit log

2015-06-30 File/folder organization
    [BearringBig1212 (repaired).stl, BearringBigREP (repaired).stl, BearringSmall1312_x_4.stl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]
2015-06-30 Many 2D/3D file changes/additions
    [1.3dm, 2.3dm, 3.3dm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]
2015-07-29 WIP, Fritzing
    [1.3dm, 1vert.stl, BearingRevised.3dm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]
2015-07-29 WIP file cleanup
    [1vert.stl, BearingRevised.3dm, BearingRevised.stl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]
